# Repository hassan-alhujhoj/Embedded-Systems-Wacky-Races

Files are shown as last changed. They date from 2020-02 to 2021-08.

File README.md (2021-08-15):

Wacky Races Project
===================
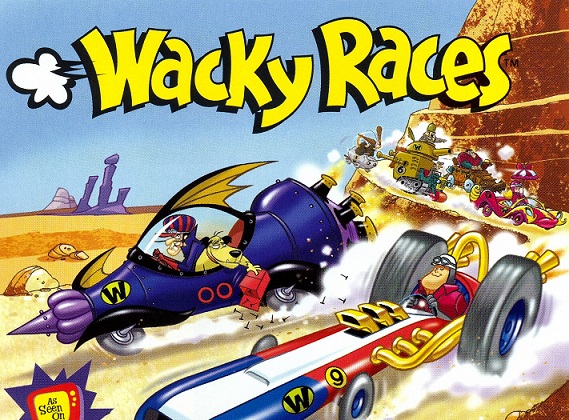
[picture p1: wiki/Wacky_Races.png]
Original_Series
.
[source](http://www.ps1fun.com/wacky-races)

Description
===========
This project was inspired by the infamous cartoon series Wacky Races which involves designing unique vehicles for each character that match their personalities. This project aimed to bring the series into an embedded systems reality.

The purpose of this assignment was to design, build, and program an embedded system using Atmel SAM4S8 microcontroller and surface mount technology. The goal of this assignment was to build the Wacky Racer (the driver board) and Wacky Hat (the vehicle controller) in Altium Designer, to populate the board using surface mount technologies (SMT), and to program the two boards in C to communicate with each other via nRF24 radio module.

This project was split into two groups: one group is responsible for the hat while the other work on the racer. Each group needed to design their board and work concurrently when collaboration is needed.

Project Outcome
===============
Participate in a Wacky Race and battle against other groups to eliminate them from the race.

Project Diagram
===============
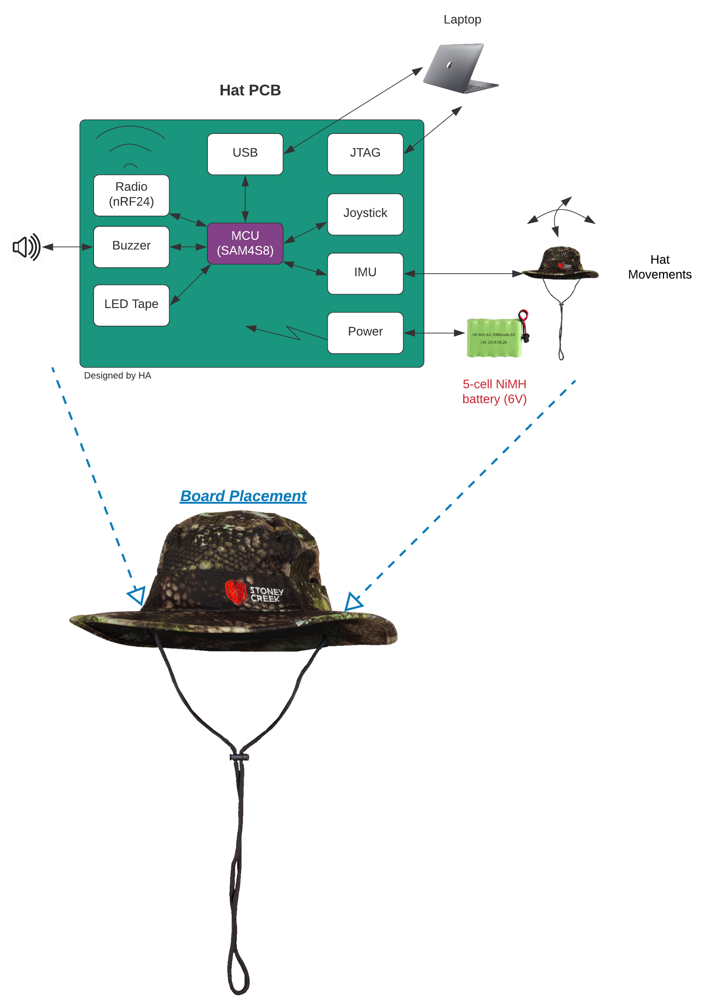
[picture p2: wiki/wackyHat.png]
hat

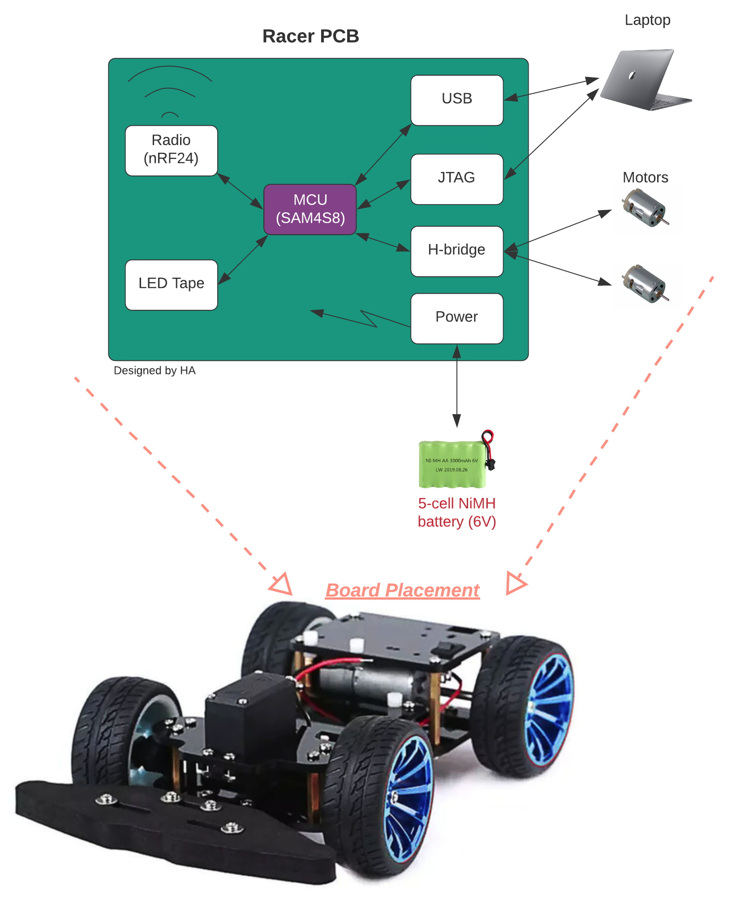
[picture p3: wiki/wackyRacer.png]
racer


Requirements
============
## Wacky Racer
* Must design a 4-layer PCB of dimension 85mmX64mm
* Use a USB interface for debugging
* Use a serial wire debug interface for MCU programming/debugging
* Must include an addequate fusing and reverse polarity protection
* Must have a sleep button
* Have afour jumber selected radio channels
* Interface with Wacky Hat board with a Nordic nRF24 SMD radio module
* Must include a low-battery-LED indicator
* Must be decorated with an LED tape controlled by the MCU
* Must regulate the nominal battery voltage to 5V with ADP2302ARDZ-50
* Drive the motors using H-briges (DRV8833)
* Use USB and JTAG interfaces for debugging

## Wacky Hat
* Must design a 4-layer PCB of dimension 85mmX64mm
* Use a USB interface for debugging
* Use a serial wire debug interface for MCU programming/debugging
* Must include an addequate fusing and reverse polarity protection
* Must have a sleep button
* Have afour jumber selected radio channels
* Interface with Wacky Hat board with a Nordic nRF24 SMD radio module
* Must include a low-battery-LED indicator
* Must be decorated with an LED tape controlled by the MCU
* Must regulate the nominal battery voltage to 5V with ADP2302ARDZ-50
* Use I2C IMU (MPU-9250) for head motion detection
* Use USB and JTAG interfaces for debugging

PCB Design
==========
doc_1doc_1  
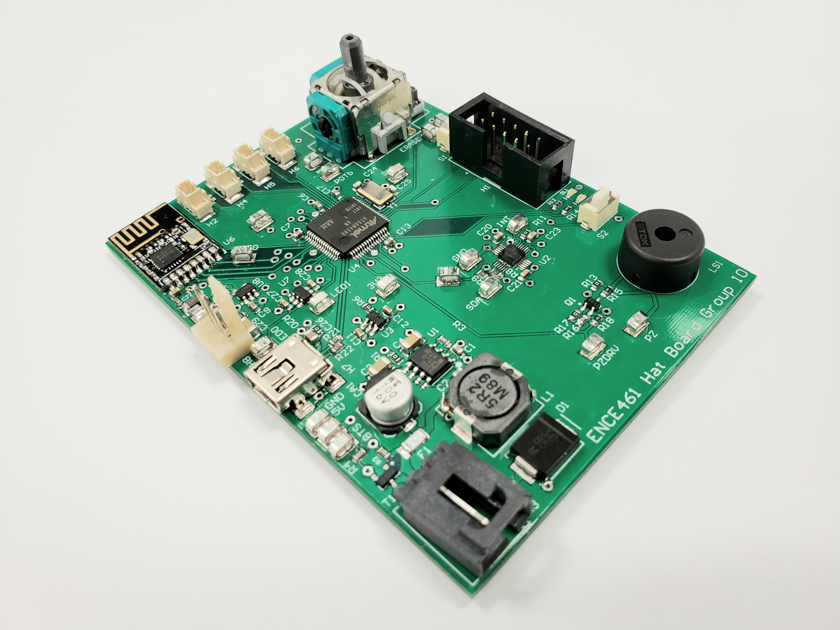
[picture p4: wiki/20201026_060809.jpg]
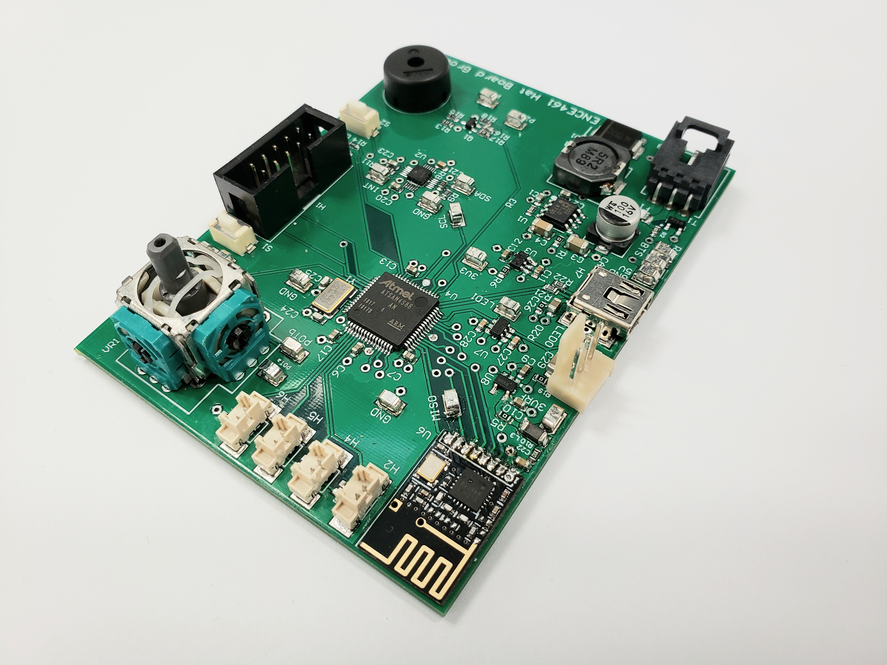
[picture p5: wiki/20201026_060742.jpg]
  

Contributors
============
* [Hassan Alhujhoj](https://github.com/hassan-alhujhoj)
* [Marcus Hughan](https://github.com/marcusHughan)
* [Nathan James](https://github.com/natedawgsnz)
* [Abdullah Naeem](https://eng-git.canterbury.ac.nz/ana104)

License
=======
Licensed under [MIT License](LICENSE)

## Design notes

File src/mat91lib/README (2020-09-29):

This library provides low level hardware abstraction for an AT91SAM7S
ARM microcontroller (with an ARM7TDMI ARM Thumb Processor).

These routines are design primarily for a bare-metal system.  The
philosophy is not to block (well at not least for long).

TODO
Convert files to use doxygen markup

Perhaps use CMSIS - Cortex Microcontroller Software Interface Standard

A note on handles.  These are designed to be opaque pointers or
integers and to provide a consistent interface.  This improves
portability but can be unnecessarily confusing.  Moreover, opaque
pointers hinder debugging.  In hindsight, I'd remove the opacity.

From a consistent interface point of view, the only exception is
pio_t.  Dereferencing a pointer stymies many optimisations, especially
for low performance microcontrollers.

adc_t
pwm_t
spi_t
ssc_t
tc_t
udp_t
usart_t

pio_t  (uint32)

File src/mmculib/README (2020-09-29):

Introduction:

This library (mmculib) contains a number of microprocessor independent
device drivers and miscellaneous functions.  It is primarily designed
for a bare-metal system.  mmculib relies on another library (such as
mat91lib) for microprocessor dependent support (such as low level
drivers for PIO, PWM. timer-counter (TC), etc.).

Compilation:

Here's an example of a Makefile to generate a program for the SAM4S16B
using mmculib and mat91lib.

# Executable file to create.
TARGET = target.bin

SRC = target.c foo.c bar.c

# Drivers from mmculib to use
DRIVERS = usb_cdc busart
# Peripherals from mat91lib to use
PERIPHERALS = ssc tc adc ac

# Microcontroller variety
MCU = SAM4S16B
# Link for ROM or RAM
RUN_MODE = ROM
# Optimisation options
OPT = -Os
# Path to mmculib top-level
MMCULIB_DIR = ../../mmculib
include $(MMCULIB_DIR)/mmculib.mk

The heavy-lifting is performed by the makefile fragment, mmculib.mk.
This automatically includes mat91lib.mk and the makefile fragments for
each driver and peripheral.

Other makefile variables that can be set to control the compilation are:
INCLUDES --- A list of paths to search for include files
VPATH    --- A list of paths to search for source files
CFLAGS   --- C compilation flags

Device driver API guidelines:

Each driver should support the following block read/write functions
where the addr parameter is optional.  Note the buffer is type void *
so that any object can be read/written without casting.  Len is the
transfer size in bytes.  The return value is the actual number of
bytes read or written.  Dev is a handle created by foo_init.  The
readv and writev forms are for reading/writing using a vector of
descriptors.  These forms are useful for coalescing I/O to minimise
writes (say to flash memory) or for atomic operations.

foo_ret_t
foo_read (foo_t dev, foo_addr_t addr, void *buffer, foo_size_t len);

foo_ret_t
foo_write (foo_t dev, foo_addr_t addr, const void *buffer, foo_size_t len);

foo_ret_t
foo_writev (foo_t dev, foo_addr_t addr, iovec_t *iov, iovec_count_t iov_count);

foo_ret_t
foo_readv (foo_t dev, foo_addr_t addr, iovec_t *iov, iovec_count_t iov_count);

Note, these routines should not block, well only for a very short time.

bits.h			Bit twidding macros
busart.c		Buffered USART driver
busart.h
button.c		Button/switch debouncing
button.h
buttons.c		Multiple button/switch debouncing
buttons.h
chaser.c		Sequenced flashing, uses flasher
chaser.h
ds18b20.c		Dallas one wire temperature sensor driver
ds18b20.h
ds2450.c		Dallas one wire ADC driver
ds2450.h
dscrc16.c		Dallas one wire 16 bit CRC
dscrc16.h
dscrc8.c		Dallas one wire 8 bit CRC
dscrc8.h
flasher.c		Generalised software PWM/flashing support
flasher.h
flasher_tweak.c		Run-time flasher manipulation
flasher_tweak.h
font.h			Font definition
isqrt16.c		16 bit integer square root
isqrt32.c		32 bit integer square root
lcd.c			HD44780/KS0066 LCD driver
lcd.h				
led.c			Simple LED driver
led_flash.c		LED flashing support
led_flash.h
led.h
lmatrix.c		LED matrix driver
lmatrix.h
mmelody.c		Interpret and sequence monophonic melodies
mmelody.h
mpwm.c
mpwm.h
mtext.c			Moving text driver
mtext.h
muxleds.c		Multiplexed LED driver
muxleds.h
nmea.c			NMEA string printing
nmea.h
nrf2401.c		Nordic RF driver
nrf2401.h
nrf_config.h
pga.c			Microchip PGA driver
pga.h		
piezo_beep.c		Piezo beep routines
piezo_beep.h
piezo.c			Simple piezo driver
piezo.h
rf.c			Generalised RF driver
rf.h
rf_master.c		Generalised RF master support
rf_slave.c		Generalised RF slave support
ring.c			Ring buffer
ring.h
scroller.c		Bit-mapped text scroller
scroller.h
s_eeprom.c		SPI EEPROM driver
s_eeprom.h
seq.c			Simple sequencer
seq.h
spwm.c
spwm.h
squeaker.c		Simple monophonic tune player
squeaker.h
stext.c			Simple text scroller (use mtext now)
stext.h
ticker.c		Simple polled timer
ticker.h
tweeter.c		PWM control of a piezo tweeter
tweeter.h
u1wire.c		Dallas universal one wire bus support
u1wire_debug.c		Dallas universal one wire bus debugging
u1wire_discover.c       Dallas universal one wire bus device discovery
u1wire_discover.h
u1wire.h
uint16toa.c		16-bit unsigned integer -> ASCII
uint16toa.h
uint8toa.c		8-bit unsigned integer -> ASCII
uint8toa.h

TODO
Convert files to use doxygen markup

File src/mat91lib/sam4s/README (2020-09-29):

Each MCU in sam4sxxxx.h defines SPI, PWM, TC0, for example 

#define SPI        ((Spi    *)0x40008000U)

The data structures are defined in Atmel/components/component_spi.h etc.

This is equivalent to the old AT91C_BASE_SPI

#define AT91C_BASE_SPI       (AT91_CAST(AT91PS_SPI) 	0xFFFE0000)

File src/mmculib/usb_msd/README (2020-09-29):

Perhaps the usb_sbc module is too coupled to usb_bot.

usb_bot requires callbacks for usb reading and writing.  Perhaps this
should be changed to non-blocking I/O.

usb_bot.c has too much MSD specific handling, for example, setup
requests, cbw, and csw stuff.

TODO, if the USB connection times out, say by using gdb, then
removing and reconnecting the USB does not properly work.

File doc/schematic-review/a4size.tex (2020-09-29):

% A4 210 mm x 298 mm
\pagestyle{plain}			% the default anyway
\pagenumbering{arabic}
\setlength{\oddsidemargin}{0mm}
\setlength{\evensidemargin}{-14mm}
\setlength{\marginparwidth}{0cm}
\setlength{\marginparsep}{0cm}
\setlength{\topmargin}{2mm}
\setlength{\headheight}{0mm}
\setlength{\headsep}{0cm}
\setlength{\textheight}{240mm}
\setlength{\textwidth}{168mm}
\setlength{\topskip}{0mm}
\setlength{\footskip}{10mm}
%
\setlength{\parindent}{8ex}

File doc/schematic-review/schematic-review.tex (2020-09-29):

\documentclass[a4paper, 12pt]{article}
\input a4size

\title{ENCE461 Schematic Review}
\author{M.P. Hayes}
\date{}

\begin{document}
\maketitle

\begin{center}
\textbf{Bring your schematics, printed on A3 paper}  
\end{center}

\section{Common}

\begin{enumerate}
\item Student names and group number in title block

\item Battery fusing (this is mandatory)

\item Can be powered from USB

\item Use serial wire debug interface for programming  

\item 3.3\,V MCU regulator can be back driven

\item Short circuit protection for MCU pio pins going to external headers

\item Battery voltage monitoring

\item Do the analogue inputs to the MCU exceed 3.3 V?  

\item LEDs for debugging  

\item Jumpers for mode configuration

\item Pullup resistors on TWI bus  
  
\item Test points

\item Ground test points

\item Game board interface connects to USART (TXD0/PA6 or TXD1/PA22 to
  TXD, RXD0/PA5 or RXD1/PA21 to RXD)

\item USB has series termination resistors

\item VBUS detection through voltage divider to PIO pin.  This is
  needed so that the MCU can tell when USB is plugged in or removed.
  You will also need diodes (or jumpers) so that the USB 5\,V can be
  connected to the 5\,V from the switching regulator.

\item Power supply filtering for radio (recommend ferrite bead or
  resistor in series with power rail with parallel capacitor)

\item The radio needs to be connected to SPI pins (MISO/PA12,
  MOSI/PA13, SCK/PA14)

\item TWI uses TWCK0/PA4 and TWD0/PA3 or TWCK1/PB5 and TWD1/PB4.
  
\item SAM4S erase pin on testpoint

\item SAM4S has 12\,MHz crystal

\item Reset button connected to NRST pin

\item Power on/off button connected to WKUPn pin

\item Avoid PB4--PB5 for general I/O (they default to JTAG pins on
  reset but can be reconfigured in software)

\item Have external pull-down resistors to ensure chips are disabled on
  power-up

\item Have a few spare PIO pins connected to pads for last minute mods.  
  
\end{enumerate}

\section{Hat board}

\begin{enumerate}
\item Battery can be charged from USB
  
\item Fall-back option if IMU does not work

\item Nav-switch or joystick for remote control  
  
\item Drive circuit for piezo tweeter

\end{enumerate}

\section{Racer board}

\begin{enumerate}
\item Fall-back option to drive motors via servo interface using PWM
  if H-bridge driver fails
  
\item MOSFET(s) for actuator (if use p-channel MOSFET need transistor
  to provide sufficient gate voltage to turn MOSFET off)

\item H-bridge driven by four PWM signals (it is best to use PWMHx,
  note PWMLx and PWMHx are complementary)

\item H-bridge AISEN and BISEN pins connected to ground (unless using
  current control)

\end{enumerate}

\end{document}

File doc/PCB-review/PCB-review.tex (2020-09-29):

\documentclass[a4paper, 12pt]{article}
\usepackage{url}

\input a4size

\title{ENCE461 PCB Review}
%\author{M.P. Hayes}
\author{}
\date{}

\begin{document}
\maketitle

\begin{center}
  \textbf{Bring this checklist, annotated with ticks or question
    marks, a printout of your new schematics, and the schematics
    annotated at the schematic rewiew.}
\end{center}

\section*{Schematic}

\begin{enumerate}
\item Battery is fused before any other electrical connection

\item Battery has reverse polarity protection (hat board only)

\item 3.3\,V for game board is provided by LDO regulator connected to
  battery on hat board

\item Radio has power supply filtering

\item Game board RX pin (3) connected to SAM4S USART RXD (PA5, PA21), and TX pin
  (5) connected to SAM4S USART TXD.

\end{enumerate}

\section*{Silk screen layer}

\begin{enumerate}
\item Has group number

\item Has student names

\item Has clearly labelled test points

\item Has clearly labelled battery polarity for hat board

\item Has clearly labelled connectors  

\end{enumerate}

\section*{Mechanical}

\begin{enumerate}
\item Drill sizes meet requirements (min 0.3, steps of 0.1)

\item USB connector hangs over edge correctly
  
\item Radio antenna hangs over edge or there are cut-outs in the PCB planes  
\end{enumerate}

\pagebreak

\section*{Plane layers}

\begin{enumerate}
\item Has a ground plane
  
\item The ground plane is connected to the GND net

\item Has a power plane (this can be partitioned)

\item The power planes are connected to the appropriate power nets

\item Has cut outs for the radio antenna if the antenna does not hang
  over edge
\end{enumerate}

\section*{Signal layer}

\begin{enumerate}
\item All vias go from top to bottom layers

\item There are no long power/ground traces to planes (use more vias)
  
\item Large vias and wide traces are used for power/ground and
  high-current traces
  
\item IC pins are not connected between the pads
  
\item SPI, I2C, PWM, and UART signals do not run over gaps in a plane

\item SPI, I2C, PWM, and UART signals do not change layers more than twice

\item Ground test points are positioned for ease of use
\end{enumerate}

\section*{Design rule check}

\begin{enumerate}
\item There are no clearance violations when performing a design rule check

\item There are no trace width violations when performing a design rule check  

\item There are no unrouted nets  
\end{enumerate}  

Note, Altium gets confused with the pad to plane check when adding
decoupling caps, so ignore warnings with distances of 2.5\,m.

\section*{Further checks}

See
\url{http://ecewiki.elec.canterbury.ac.nz/mediawiki/index.php/PCB_guidelines}
and
\url{http://ecewiki.elec.canterbury.ac.nz/mediawiki/index.php/PCB_advanced_guidelines}.

\end{document}

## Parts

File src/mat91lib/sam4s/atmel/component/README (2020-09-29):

These files define a structure for each peripheral but not their bases
addresses.  The structures are named Spi, Pwm, etc.

Spi is equivalent to the old AT91PS_SPI.

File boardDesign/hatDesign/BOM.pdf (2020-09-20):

Bill of Materials | Bill of Materials for PCB Document [HatBoard_Group10.PcbDoc]
Source Data From: | | HatBoard_Group10.PcbDoc
Project: | | WackyRacesHat.PrjPcb
Variant: | | None
Creation Date: | 22/06/2020 | 11:10 PM
Print Date: | 22-Jun-20 | 11:11:22 PM
Footprint | Comment | LibRef | Designator | Description | Quantity
CAPC1608L | 100nF | CC_100nF_0603 | C1, C2, C5, C6, C7, C8, C13, C14, C15, C16, C17, C19, C20, C23 | CAP CER 100nF X7R +-10% 50V 0603 | 14
CAPC3216L | 22uF | CC_22uF_1206 | C3, C4, C29 | CAP CER 22uF Y5V -20% +80% 10V 1206 | 3
CAPC1608L | 1uF | CC_1uF_0603 | C9, C10, C11, C12 | CAP CER 1uF Y5V -20% +80% 16V 0603 | 4
CAPC1608N | 4.7uF | CC_4.7uF_0603 | C18, C26 | CAP CER 4.7uF X5R +-20% 10V 0603 | 2
CAPC1608L | 10nF | CC_10nF_0603 | C21, C27, C28 | CAP CER 10nF X7R +-10% 50V 0603 | 3
CAPC1608L | 10uF | CC_10uF_0603 | C22 | CAP CER 10UF X5R +-20% 6V3 0603 | 1
CAPC1608L | 27pF | CC_27pF_0603 | C24, C25 | CAP CER 27pF NPO/COG +-5% 50V 0603 | 2
NICH-1 | 100uF/16V | CA_100uF_16V | CA1 | CAP ALUM 100uF 16V SMD | 1
SMC | VS-30BQ015-M3/9AT | DS_VS-30BQ015-M3 | D1 | DIODE, SCHOTTKY, 3A, 15V, DO-214AB / SMC | 1
WL-SMCW0603 | Bright Green | DL_150060VS75000 | DL1 | LED Bright Green 40mcd 0603 SMD | 1
WL-SMCW0603 | Red | DL_150060RS75000 | DL2 | LED Red 250mcd 0603 SMD | 1
RESC3216N | 5A | FS_Fuse_5.0A | F1 | Fuse 5.0A Fast Acting 1206 SMD | 1
IDC2.54-V10D | Header 5X2 Vert | JA_HDR_IDC_5X2_VERT | H1 | IDC Header, 2,54mm, 10-Pin, Vert | 1
SD-53398-0219 | SMD Vert 1.25mm | JB_53398-02 | H2, H4, H5, H6 | Header_Vert_2Pos_1.25mm_125V@1A_SMT | 4
BATT_HEADER_3POS | Battery_HEADER_3pin | Battery_HEADER_3pin | H3 | 3Pin Header 2.54mm spacing | 1
USB/SM0.8-6H5 | JS_USB_MINI_B | JS_USB_MINI_B_SMT | H7 | USB 2.0, Right Angle, SMT, B Type, Receptacle, 5 Position, | 1
HEADER_3POS | HEADER_3 | HEADER_3 | H8 | 3Pin Header 2.54mm spacing | 1
INDUCTOR5u2 | IND 5.2UH 6A | CDRH104RNP-5R2NC | L1 | FIXED IND 5.2UH 6A 22 MOHM SMD | 1
INDC3216L | 1A max, Idc 0.3R, | IN_Ferrite-Bead | L2, L3 | Ferrite Bead, Rdc 0.3R, Z100MHZ 600R, Imax 1A, SMD 1206 | 2
XDCR_PS1240P02BT | PS1240P02BT | PS1240P02BT | LS1 | Buzzers Transducer, Externally Driven Piezo 3V 4kHz 60dB @ 3V, 10cm Through Hole PC Pins | 1
SOT323_M | BC817W | TB_BC817W | Q1 | NPN GP Bipolar Transistor 45V 500mA SOT323 | 1
RESC1608L | 0R | RS_0R0 | R1, R5, R6, R11, R13, R17, R19, R20 | RES 0.0 OHM 1/10W 5% 0603 SMD | 8
RESC1608L | 200K | RS_200K | R2 | RES 200K OHM 1/10W 5% 0603 SMD | 1
RESC1608L | 100K | RS_100K | R3, R4 | RES 100K OHM 1/10W 5% 0603 SMD | 2
RESC3216L | 1R | RT_1R | R7 | RES 1R OHM 1/4W 5% 1206 SMD | 1
RESC1608L | 2K2 | RS_2K2 | R8, R9 | RES 2.2K OHM 1/10W 5% 0603 SMD | 2
RESC1608L | 10R | RS_10R | R10, R16 | RES 10 OHM 1/10W 5% 0603 SMD | 2
RESC1608L | 470R | RS_470R | R12 | RES 470 OHM 1/10W 5% 0603 SMD | 1
RESC1608L | 680R | RS_680R | R14 | RES 680 OHM 1/10W 5% 0603 SMD | 1
RESC1608L | 1K | RS_1K | R15, R18 | RES 1.0K OHM 1/10W 5% 0603 SMD | 2
RESC1608L | 27R | RS_27R | R21, R22 | RES 27 OHM 1/10W 5% 0603 SMD | 2
EVQPNF05M | EVQPNF05M | WS_EVQPNF05M | S1, S2 | Panasonic 6 x 3.5mm SMD Light Touch Switch Type SMD | 2
SOT23_L | BSH105,215 | TM_BSH105 | T1 | MOSFET N-CH 20V 1.05A SOT-23 | 1
RD_8_1 | ADP2302ARDZ-5.0 BUCK | ADP2302ARDZ-5.0-R7 | U1 | IC REG BUCK 5V 2A 8SOIC | 1
QUAD24 | MPU-9250 | MPU-9250 | U2 | 9 axis IMU | 1
SOT95P280X145-5N | CAT6219-330TDGT3 | SV_CAT6219-330TDGT3 | U3, U8 | IC REG LIN 3.3V 500MA TSOT23-5 | 2
LQFP64_L | ATSAM4S8BA-ANR | SE_ATSAM4S16BA-MU | U4 | IC MCU 32BIT 512KB FLASH 64LQFP | 1
NRF24 | nRF24 SMD | NRF24 | U6 | nRF24 SMD Module | 1
SOT23-6_N | SN74LVC1T45 | SN74LVC1T45 | U7 | 1.8V - 5V level converter | 1
Joystick_Sw | Joystick 10k with Sw | Joystick 10k with Sw | VR1 | JOYSTICK 10K OHM 2 AXIS TH | 1
6.0X3.5-4 | 12MHz | XT_CRYSTAL_12MHz_18pF | Y1 | CRYSTAL 12MHZ 18PF 6X3.5mm SMD | 1
| | | | | 81
Approved | | Notes
Altium Limited Confidential | 22/06/2020 | Page 1

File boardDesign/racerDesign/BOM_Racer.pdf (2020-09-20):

Bill of Materials | Bill of Materials for PCB Document [WackyRacerPCB.PcbDoc]
Source Data From: | | WackyRacerPCB.PcbDoc
Project: | | WackyRacerDesign.PrjPcb
Variant: | | None
Creation Date: | 18/06/2020 | 4:25 PM
Print Date: | 18-Jun-20 | 4:25:29 PM
Footprint | Comment | LibRef | Designator | Description | Quantity
SOT95P280X145-5N | CAT6219-330TDGT3 | SV_CAT6219-330TDGT3 | 3V3_REG, 3V3RF_REG | IC REG LIN 3.3V 500MA TSOT23-5 | 2
RD_8_1 | ADP2302ARDZ-5.0 BUCK | ADP2302ARDZ-5.0-R7 | BUCK | IC REG BUCK 5V 2A 8SOIC | 1
MOLEX_KK_2_HDR | 2 Pin Molex KK HDR | JA_MOLEX_KK_2POS | Bumper, CH1, CH2, CH3, CH4, M_1, M_2, M_3 | CONN HEADER 2POS 2.54mm VERT_Thru Hole | 8
CAPC1608L | 10uF | CC_10uF_0603 | C1, C4, C10, C25 | CAP CER 10UF X5R +-20% 6V3 0603 | 4
CAPC1608L | 27nF | CC_27nF_0603 | C2, C3 | CAP CER 27nF X7R +-10% 50V 0603 | 2
CAPC1608L | 100nF | CC_100nF_0603 | C5, C12, C13, C14, C15, C16, C17, C18, C19, C22, C24, C26, C30, C31 | CAP CER 100nF X7R +-10% 50V 0603 | 14
CAPC3216L | 22uF | CC_22uF_1206 | C6, C7 | CAP CER 22uF Y5V -20% +80% 10V 1206 | 2
CAPAE6666X77M | 100µF/25V | CA_100uF_25V | C8 | CAP ALUM 100UF 25V 20% SMD | 1
CAPC1608L | 10nF | CC_10nF_0603 | C9 | CAP CER 10nF X7R +-10% 50V 0603 | 1
CAPC1608L | 2.2uF | CC_2.2uF_0603 | C11, C27 | CAP CER 2.2uF X5R +-20% 10V 0603 | 2
CAPC1608L | 1uF | CC_1uF_0603 | C20, C21, C28, C29 | CAP CER 1uF Y5V -20% +80% 16V 0603 | 4
CAPC1608N | 4.7uF | CC_4.7uF_0603 | C23, C32 | CAP CER 4.7uF X5R +-20% 10V 0603 | 2
SMC | SCHOTTKY 30V 4A | MBRS330T3G | D1 | DIODE SCHOTTKY 30V 4A SMC | 1
WL-SMCW0603 | Dark Green | DL_150060GS75000 | DL1 | LED Dk Green 430mcd 0603 SMD | 1
WL-SMCW0603 | Red | DL_150060RS75000 | DL2 | LED Red 250mcd 0603 SMD | 1
RESC3216N | 5A | FS_Fuse_5.0A | F1 | Fuse 5.0A Fast Acting 1206 SMD | 1
IDC2.54-V10D | Header 5X2 Vert | JA_HDR_IDC_5X2_VERT | H1 | IDC Header, 2,54mm, 10-Pin, Vert | 1
BATT_HEADER_3POS | Battery_HEADER_3pin | Battery_HEADER_3pin | H3 | 3Pin Header 2.54mm spacing | 1
HEADER_3POS | HEADER_3 | HEADER_3 | H4 | 3Pin Header 2.54mm spacing | 1
HTSOP16 | DRV8833 | DRV8833 | H-Bridge_1, H-Bridge_2 | Dual H-Bridge Motor Driver 1.5A | 2
INDC3216L | 1A max, Idc 0.3R, | IN_Ferrite-Bead | L1, L3 | Ferrite Bead, Rdc 0.3R, Z100MHZ 600R, Imax 1A, SMD 1206 | 2
INDUCTOR5u2 | IND 5.2UH 6A | CDRH104RNP-5R2NC | L2 | FIXED IND 5.2UH 6A 22 MOHM SMD | 1
TP_0603 | =Value | TP_0603 | LED_IN1, MOSI, SCK | Test Point 1.65X0.9X1.2mm SMD | 3
MOLEX_KK_3_HDR | 3 Pin Molex KK Hdr | JA_MOLEX_KK_3POS | LED_TAPE | CONN HEADER 3POS 2.54mm VERT_Thru Hole | 1
SOT23-6_N | SN74LVC1T45 | SN74LVC1T45 | LVL_CON | 1.8V - 5V level converter | 1
TP_0603 | TP_0603 | TP_0603 | MISO | Test Point 1.65X0.9X1.2mm SMD | 1
NRF24 | nRF24 SMD | NRF24 | nRF24 | nRF24 SMD Module | 1
SOT23_L | SSM3J328R,LF | TM_SSM3J328R | Q1 | MOSFET P-CH 20V 6A SOT23-3 | 1
RESC1608L | 10R | RS_10R | R1 | RES 10 OHM 1/10W 5% 0603 SMD | 1
RESC1608L | 27R | RS_27R | R2, R3 | RES 27 OHM 1/10W 5% 0603 SMD | 2
RESC1608L | 100R | RS_100R | R4, R6 | RES 100 OHM 1/10W 5% 0603 SMD | 2
RESC1608L | 1K3 | RS_1K3 | R7 | RES 1.3K OHM 1/10W 5% 0603 SMD | 1
RESC1608L | 100K | RS_100K | R8, R9 | RES 100K OHM 1/10W 5% 0603 SMD | 2
RESC1608L | 0R | RS_0R0 | R10, R11, R13, R14 | RES 0.0 OHM 1/10W 5% 0603 SMD | 4
RESC3216L | 1R | RT_1R | R12 | RES 1R OHM 1/4W 5% 1206 SMD | 1
RESC1608L | 470K | RS_27R, RS_47R | R15, R19 | RES 27 OHM 1/10W 5% 0603 SMD, RES 47 OHM 1/10W 5% 0603 SMD | 2
RESC1608L | 270K | RS_27R, RS_47R | R16, R18 | RES 27 OHM 1/10W 5% 0603 SMD, RES 47 OHM 1/10W 5% 0603 SMD | 2
RESC1608L | 10K | RS_10K | R17, R20 | RES 10.0K OHM 1/10W 5% 0603 SMD | 2
EVQPNF05M | EVQPNF05M | WS_EVQPNF05M | S1, S2 | Panasonic 6 x 3.5mm SMD Light Touch Switch Type SMD | 2
LQFP64_L | ATSAM4S8BA-ANR | SE_ATSAM4S16BA-MU | U1 | IC MCU 32BIT 512KB FLASH 64LQFP | 1
MOLEX_KK_4_HDR | Ultrasonic Sensor Connector | JA_MOLEX_KK_4POS | US | CONN HEADER 4POS 2.54mm VERT_Thru Hole | 1
FCI_USB_10118194-0001LF | JS_USB_MICRO_B | JS_USB_MICRO_B_SMT | USB | CONN USB MICRO B RECPT SMT R/A | 1
6.0X3.5-4 | 12MHz | XT_CRYSTAL_12MHz_18pF | Y1 | CRYSTAL 12MHZ 18PF 6X3.5mm SMD | 1
| | | | | 88
Approved | | Notes
Altium Limited Confidential | 18/06/2020 | Page 1

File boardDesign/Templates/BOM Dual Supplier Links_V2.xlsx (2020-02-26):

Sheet: BOM Report
Bill of Materials |  |  | Field=Title
Source Data From: |  | Field=DataSourceFileName
Project: |  | Field=ProjectFileName
Variant: |  | Field=VariantName
Creation Date: | Field=ReportDate | Field=ReportTime
Print Date: | 2015-03-04 | 16:44:09
Production Quantity: | Field=ProductionQuantity
Currency | Field=Currency
Column=Footprint | Column=Comment | Column=LibRef | Column=Designator | Column=Description | Column=Quantity | Column=Supplier 1 | Column=Supplier Part Number 1 | Column=Supplier 2 | Column=Supplier Part Number 2 | Column=Manufacturer | Column=Manufacturer Part Number | Column=Manufacturer PN | Column=Supplier Stock 1 | Column=Supplier Stock 2
 |  |  |  |  | 0
Approved |  | Notes

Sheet: Project Information
Project Full Path | Field=ProjectFullPath
Project Filename | Field=ProjectFileName
Variant Name | Field=VariantName
Data-Source Filename | Field=DataSourceFileName
Data-Source Full Path | Field=DataSourceFullPath
Title | Field=Title
Total Quantity | Field=TotalQuantity
Report Time | Field=ReportTime
Report Date | Field=ReportDate
Report Date & Tine | Field=ReportDateTime
Output Name | Field=OutputName
Output Type | Field=OutputType
Output Generator Name | Field=GeneratorName
Output Generator Description | Field=GeneratorDescription

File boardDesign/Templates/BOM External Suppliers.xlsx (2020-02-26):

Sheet: BOM Report
Bill of Materials |  |  | Field=Title | BOM of externally supplied components
Source Data From: |  | Field=DataSourceFileName
Project: |  | Field=ProjectFileName
Variant: |  | Field=VariantName
Creation Date: | Field=ReportDate | Field=ReportTime
Print Date: | 2013-08-14 | 15:08:35
Column=LibRef | Column=Comment | Column=Footprint | Column=Designator | Column=Description | Column=Quantity | Column=Manufacturer | Column=Manufacturer Part Number 1 | Column=Supplier 1 | Column=Supplier Part Number 1 | Column=Supplier 2 | Column=Supplier Part Number 2 | Column=Supplier 3 | Supplier Part Number 3
 |  |  |  |  | 0
Approved |  | Notes

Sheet: Project Information
Project Full Path | Field=ProjectFullPath
Project Filename | Field=ProjectFileName
Variant Name | Field=VariantName
Data-Source Filename | Field=DataSourceFileName
Data-Source Full Path | Field=DataSourceFullPath
Title | Field=Title
Total Quantity | Field=TotalQuantity
Report Time | Field=ReportTime
Report Date | Field=ReportDate
Report Date & Tine | Field=ReportDateTime
Output Name | Field=OutputName
Output Type | Field=OutputType
Output Generator Name | Field=GeneratorName
Output Generator Description | Field=GeneratorDescription

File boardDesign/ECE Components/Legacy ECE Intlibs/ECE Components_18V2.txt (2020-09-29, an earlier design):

Created using AD18.1.7 (Build 191)
Tested using AD16.1.10 (Build 233) - 2018 ECE Dept installed version.

28 AUGUST 2018
***ECE Components_18V2.IntLib***
ADD - FS_FUSE_10A smd fuse 
FIX - JA_TERM_BLK_HDR2 - E14 manufacturer & part numbers mixed. Added Digikey data
DEL - Remove 100nF 0402 cap.
DEL - DS_VS_30BQD015TRPBF - obsolete
ADD - DS_VS_30BQ015-M3 - replacement for DS_VS_30BQD015TRPBF
FIX - TM_SSM3J328R - update parameters VDSS & ID(dc). Fix part#. Add datasheet
FIX - WS_EVQPNF05M - increase footprint pads 2x1.6 -> 2.5x1.6. Allows rework.
FIX - FS_FUSE_5.0A - obsolete, remove old & add new part data & links
FIX - DR_BAS16TT1G - Fix E14 part #, add  Digikey data
FIX - XT_CRYSTAL - correct the Digikey supplier information + links
FIX - WS_SKUDBE010 - Nav switch - correct footprint pad spacing
ADD - TP_1206 - add 3d model
DEL - JP_1613 14 DC socket - obsolete
ADD - JP_PJ-002AH-SMT-TR - replaces JP_1613 14. 
FIX - JP_PJ-002AH-SMT-TR - Redraw schematic symbol - this was incorrect on obsolete part also (switching is on outer barrel not inner pin).
FIX - CA_470uF_16V - replace incorrect E14 parameters - add Digikey part info
FIX - CA_1000uF_16V - add Digikey info
FIX - JS_USB_MICRO_B_SMT - corrected footprint minimum width violation. Improved pad shape on GNDs for better strain relief and easier rework. Adj silkscreen.
ADD - JA_HDR_IDC_3X2_VERT - 6 PIN 0.1" IDC through hole connector + supplier data
ADD - IDC2.54-V06D 6PIN-IDC footprint and 3D model - Linked to JA_HDR_IDC_3x2_VERT
FIX - SV_TLV1117-33CDC add note to schematic symbol that warns about relatively high Vdropout at full load
FIX - SV_TLV1117-50CDC add note to schematic symbol that warns about relatively high Vdropout at full load

Previous updates:

***ECE_Components_16_2.IntLib***
-JB_IDC_BOX_HDR_10, schematic symbol pinout corrected
-SV_LD29300 removed - obsolete

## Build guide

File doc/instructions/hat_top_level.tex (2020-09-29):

\begin{tikzpicture}[scale=0.9]
    
  \draw[black, very thick, fill=blue!50] (-2, -1) rectangle (2, 1);
    \node at (0, 0) {SAM4S};  

    % IMU
    \draw[black, very thick] (4, -1) rectangle (7, 1);
    \node at (5.5, 0) {IMU};
    \draw[triangle 45-triangle 45] (2, 0) -- (4, 0);

    % Buzzer
    \draw[black, very thick] (4, -2) rectangle (7, -4);
    \node at (5.5, -3) {Buzzer};
    \draw[-triangle 45] (2, -1) -- (4, -2);

    % LED tape
    \draw[black, very thick] (-2, 2) rectangle (2, 4);
    \node at (0, 3) {LED tape};
    \draw[triangle 45-triangle 45] (0, 1) -- (0, 2);

    % Radio
    \draw[black, very thick] (-2, -2) rectangle (2, -4);
    \node at (0, -3) {Radio};
    \draw[triangle 45-triangle 45] (0, -1) -- (0, -2);
    \draw (0.354, -4.354) arc (-45:-135:0.5);
    \draw (0.707, -4.707) arc (-45:-135:1);
    \draw (1.061, -5.061) arc (-45:-135:1.5);

    % Power
    \draw[black, very thick] (-4, 2) rectangle (-7, 4);
    \node at (-5.5, 3) {Power};
    \draw (-5, 2) -- (-5.25, 1.4) -- (-4.75, 1.6) -- (-5, 1);
    \draw (-6, 2) -- (-6.25, 1.4) -- (-5.75, 1.6) -- (-6, 1);
    
    % USB
    \draw[black, very thick] (-4, -2) rectangle (-7, -4);
    \node at (-5.5, -3) {USB};
    \draw[triangle 45-triangle 45] (-2, -1) -- (-4, -2);

\end{tikzpicture}

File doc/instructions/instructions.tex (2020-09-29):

\documentclass[11pt, a4paper]{article}
\title{Wacky Racers 2020 Instructions}
\author{Michael Hayes, Ben Mitchell}
\date{Version 3, \today}

\usepackage[margin=1in]{geometry}
\usepackage{parskip}
\usepackage{float}
\usepackage{todonotes}
\presetkeys{todonotes}{inline}{}
\usepackage{graphicx}
\usepackage[T1]{fontenc}
\usepackage{makecell}
\usepackage[breaklinks=true]{hyperref}
\usepackage{tabularx}
\usepackage{subcaption}
\usepackage{listings}
\usetikzlibrary{arrows}

\newcommand{\code}[1]{\texttt{#1}}

\begin{document}
\maketitle

\section{Introduction}

The purpose of this assignment is to design, build, and program an
embedded system using an ARM microcontroller and surface mount
technology.

The goal for each group of four students is to build a remote
controlled vehicle (the Wacky Racer) and its controller (the Wacky
Hat).  At the conclusion of the assignment there will be a dastardly race!

Each group is comprised of two sub-groups of two students.  One of
these subgroups constructs the Wacky Racer and the other constructs
the Wacky Hat.  You may be asking why is the Wacky Hat called the
Wacky Hat?  Well, a hat that controls a remote vehicle using head
motions is not an ordinary hat!

\section{Requirements}

The following requirements are mandatory if you wish to maximise your
marks.

\subsection{Wacky racer}

\begin{enumerate}
\item The chassis is to be constructed by each group.  These can be
  3-D printed, constructed from Perspex or wood, etc.  A standard
  chassis is available from the Automation Lab technician (Daniel
  Hopkins).  The electronics must be visible on top of the chassis.
\item Have a standard working bump sensor (supplied).  
\item Locomotion can only use two 6\,V DC motors (supplied).
\item Everything must be powered from a single 5-cell NiMH battery pack (supplied).
\item Use a single four layer printed circuit board of dimension 85\,mm$\times$64\,mm.
\item Use an ARM microcontroller (Atmel SAM4S8).
\item Drive the motors using H-bridges (Texas Instruments DRV8833 dual
  H-bridge is recommended).
\item Regulate the nominal battery voltage to 5\,V with a buck
  regulator IC (ADP2302ARDZ-50).
\item Be decorated with an LED tape (supplied) controlled by the MCU.
\item Use a USB interface for debugging.
\item Use a serial wire debug interface for MCU programming/debugging.
\item Have adequate battery fusing and reverse polarity protection.
\item Have a sleep button.
\item If the battery voltage drops below 5\,V, an LED should flash and high power draw devices should be disabled.
\item Interface to the Wacky Hat with a Nordic nRF24 SMD radio module.
\item Have four jumper selectable radio channels.  
\item Have a mounted RFID card (supplied) that can be read by the Wacky ramps.
\item Be humorous.    
\end{enumerate}

Each Wacky Racer can have a dastardly means of hindering another
team's Wacky Racer.  However, you cannot:
%
\begin{itemize}
\item Damage or destroy another Wacky racer
\item Damage the venue
\item Injure a spectator
\item Jam the radio signals  
\end{itemize}

\vspace{1cm}

\begin{figure}[h]
    \centering
    \input{racer_top_level.tex}
    \caption{Racer board top level diagram.}
\end{figure}

\vfill\pagebreak

\subsection{Wacky hat}

\begin{enumerate}
\item Construct a Wacky Hat that contains all the electronics.
\item Everything must be powered from a single 5-cell NiMH battery pack (supplied).  
\item Have adequate battery fusing and reverse polarity protection.
\item Use a single four layer printed circuit board of dimension 85\,mm$\times$64\,mm.  
\item Use an ARM microcontroller (Atmel SAM4S8).
\item Regulate the nominal 6\,V battery voltage to 5\,V with a buck
  regulator IC (ADP2302ARDZ-50).
\item Be decorated with an LED tape (supplied) controlled by the MCU.
\item Use an I2C IMU (MPU-9250) for head motion detection.
\item Use a USB interface for debugging.
\item Use a serial wire debug interface for MCU programming/debugging.
\item Have a joystick in case the IMU does not work.
\item Have a sleep button.
\item If the battery voltage drops below 5\,V, an LED should flash and high power draw devices should be disabled.
\item Play sound when the bumper is hit.
\item Interface to the Wacky Racer with a Nordic nRF24 SMD radio module.  
\item Have four jumper selectable radio channels.    
\item Be humorous.  
\end{enumerate}

%\vspace{1cm}

\begin{figure}[h]
  \centering
  \input{hat_top_level.tex}
  \caption{Racer hat top level diagram.}
\end{figure}

\pagebreak

\section{Assignment schedule}

The planned activities for the timetabled labs in the Embedded Systems
Lab (ESL) are:
%
\begin{flushleft}
  \begin{tabular}{ c l l }
    Week            &  Assistance  &  Assessment \\
    \hline \hline
    T1-1 & Altium tutorial 1 (schematics)  & \\
    T1-2 & Altium help       & \\
    T1-3 & Schematic review  &  Schematic submission for review (Mon. noon) \\
    T1-4 & Altium tutorial 2 (PCB) &          \\
    T1-5 & Altium help & PCB submission 1    \\
    T1-6 & Altium help & PCB submission 2    \\
    T1-7 & General     & PCB submission 3    \\ \hline
    B-1 & (break)    &                   \\
    B-2 & (break)    &                   \\
    B-3 & (break)    &                   \\ \hline
    T2-1 & General     & Blinky            \\
    T2-2 & General     & IMU/motors      \\
    T2-3 & General     & Radio control     \\    
    T2-4 & General     & Functionality     \\
    T2-5 & Competition & Competition, critique  \\
  \end{tabular}
\end{flushleft}

Notes:
%
\begin{enumerate}
\item There there may be a 6--10 day delay for the PCBs to be
  manufactured from the time of submission.  You will then need to
  book an assembly session in the SMT lab provided you have done the
  SMT lab induction.

\item Do not underestimate the blinky milestone.  It requires having a
  functional PCB with a microcontroller that turns on properly, a
  functional toolchain and the ability to download code into the
  microcontroller's flash memory.
\end{enumerate}

\section{Assessment}

The marks breakdown (max. 0x64) is:
%
\begin{flushleft}
  \begin{tabular}{ll}
    PCB submission & 0--0xa marks\\
    Blinky milestone  & 0x5 marks\\    
    IMU/motor milestone  & 0x5 marks\\
    Radio control milestone  & 0x5 marks\\
    Functional assessment & 0--0x14 marks \\
    Board inspection & 0--0x1e marks \\
    Competition & 0--0xa marks \\
    Individual critique & 0--0xf marks \\
  \end{tabular}
  
\end{flushleft}

\subsection{Milestones}

There are five milestones.  To achieve the associated marks, they must
be demonstrated to a T.A. by the end of the lab for your allotted
stream.  If you need an exception to this, see Ben Mitchell with a
\emph{very} good reason.  The milestone requirements are:
%
\begin{description}
\item [Schematic review] Submit your A3 schematic on Learn for
  review.  Lose 10 marks if you miss the submission time.

\item [PCB submission] Submit your PCB design to Learn for
  manufacture.  To encourage early submission there is a sliding scale
  for marks depending on when the PCB is submitted, see table.  After
  week 7, there is a 10 mark penalty per week.  \textbf{NB, a rushed
    PCB design will cause you more grief, more PCB rework, and a lower
    mark for the inspection.}

  \begin{tabular}{llll}
    Week & Submission day & Cut-off time  & Mark \\ \hline
    5    & Monday       & 10.00 am & 10 \\
    5    & Wednesday    & 10.00 am & 9 \\
    5    & Friday       & 10.00 am & 8 \\
    6    & Monday       & 10.00 am & 7 \\
    6    & Wednesday    & 10.00 am & 6 \\
    6    & Friday       & 10.00 am & 5  \\
    7    & Monday       & 10.00 am & 4 \\
    7    & Wednesday    & 10.00 am & 2 \\
    7    & Friday       & 10.00 am & 0 \\        
  \end{tabular}

\item [Blinky] Demonstrate that can blink an LED controlled by the SAM4S.
  
\item [IMU/motors] For the Wacky Hat, demonstrate output of IMU
  readings to a PC using USB CDC.  For the Wacky Racer, demonstrate
  control of the motors from a PC using USB CDC.

\item[Radio control] Demonstrate sending commands from the Wacky Hat
  to the Wacky Racer over a radio link.
\end{description}

\textbf{If you cannot show the functionality of a previous milestone
  during any assessment, you will fail that assessment and loose any
  marks from the previous milestone.}

\subsection{Functionality assessment}

Functionality requirements:
%
\begin{flushleft}
  \begin{tabular}{l|l}
    Wacky racer & Wacky hat \\ \hline \hline
    Blink LED                      & Blink LED \\
    Drive motors forward/backward  & Read from IMU \\
    Speed control of motors        & Calculate speeds from IMU \\
    Steering control               & Joystick control \\
    Receive radio message          & Send radio message \\
    Jumper selectable radio channel & Jumper selectable radio channel  \\    
    Dies on bump                   & Plays sound on bump \\
    Report group info to game server & Report group info to game server \\
    Low voltage indication         & Low voltage indication \\
  \end{tabular}
\end{flushleft}
%
Marks are allocated on how well things work.  Up to 5 bonus marks can
be awarded for extra functionality such as:
%
\begin{flushleft}
  \begin{tabular}{l|l}
    Wacky racer                & Wacky hat \\ \hline \hline
    Dastardly stuff            & Plays interesting sounds \\
    Sleep mode                 & Sleep mode \\
  \end{tabular}
\end{flushleft}

\subsection{Competition}

The competition is a race around an obstacle course.  Marks will be
awarded every time you pass over a Wacky Ramp in the correct order.
These ramps have an RFID card reader that will detect your Racer if
you have correctly fitted an RFID card.  The Wacky Ramps change colour
when they detect a Wacky Racer.

To be awarded any marks for the race:
%
\begin{enumerate}
\item Your vehicle must stop for at least 5\,s if the bumper is hit.

\item Your vehicle must be controlled by motions of the Wacky hat
  sitting on someone's head.
\end{enumerate}

\subsection{PCB inspection}

This is assessed after the competition.  The categories are:
%
\begin{enumerate}
\item Layout (component placement etc.)
\item Construction (tidiness, rework, etc.)
\item Testability  
\item Power supplies (routing, decoupling, etc.)
\end{enumerate}

\section{Technical stuff}

Read this section carefully.  There are clues as to how we mark your
PCBs at the end of the assignment.

\subsection{Version control}

Use version control for everything, or else!  Learning git is
frustrating but is a skill you will not regret.

Your group leader should create a forked copy of the wacky-racers-2020
git project and then add the other group members to the project.  This
can be done by:

\begin{enumerate}
\item Go to \url{https://eng-git.canterbury.ac.nz/wacky-racers/wacky-racers-2020}

\item Click `Fork' button.  This will create a copy of the main repository for the project.

\item Click on the `Settings' menu then click the `Expand' button for
`Sharing and permissions'.  Change `Project Visibility' to `Private'.

\item Click on the `Members' menu and add group members as Developers.

\item Using a bash terminal (or other useful shell), enter the command:

  \lstset{language=bash}
  \lstset{basicstyle=\ttfamily\small}
  \lstset{keywordstyle=\color{black}\ttfamily}
  \lstset{breaklines}
  
\begin{lstlisting}
  $ git clone https://eng-git.canterbury.ac.nz/your-userid/wacky-racers-2020.git wacky-racers
\end{lstlisting}

If you do not want to have to enter your password for every git
push/pull operation, you should set up ssh-keys and use:

\begin{lstlisting}[breaklines]
  $ git clone git@eng-git.canterbury.ac.nz:your-userid/wacky-racers-2020.git wacky-racers
\end{lstlisting}

\item Add a remote URL for the main repository.
%
\begin{lstlisting}[breaklines]
  $ cd wacky-racers 
  $ git remote add upstream https://eng-git.canterbury.ac.nz/wacky-racers/wacky-racers-2020.git  
\end{lstlisting}
%
Again if you do not want to manually enter your password, you can use:
%
\begin{lstlisting}[breaklines]
  $ cd wacky-racers 
  $ git remote add upstream git@eng-git.canterbury.ac.nz:wacky-racers/wacky-racers-2020.git    
\end{lstlisting}
%
If we add more demo code or tweak the instructions in the main
repository, you can get the updated stuff using:
%
\begin{lstlisting}[breaklines]
  $ git pull upstream master
\end{lstlisting}
\end{enumerate}

\subsection{Components}

\begin{enumerate}
\item We recommend that you use components in the ECE Altium library.
  These are stocked in the SMT lab.  For any other components you may
  require, see Scott Lloyd in the SMT lab.

\item The Wacky Racer batteries are Turnigy 5-cell 6\,V, 2300\,mAh,
  NiMH with a three pin JST connector.  To preserve the battery life
  it is imperative to not draw current when the battery voltage is
  below 5\,V.
\end{enumerate}

\subsection{Connectors}

\begin{enumerate}
\item USB micro or mini connector for debugging
\item 3 pin 0.1'' for LED tape (pin 1 5\,V, pin 2 signal, pin 3 ground)
\item 2 pin 0.1'' for bumper (pin 1 switch, pin 2 ground)
\item 10 pin IDE for serial wire debug  
\item 3 pin JST power connector (pin 1 GND, pin 2 VBAT, pin 3 GND)
\item motor connectors (for Racer)
\item connectors for dastardly stuff
\end{enumerate}

\subsection{Schematics}

\begin{enumerate}
\item Have a look at the
  \href{http://ecewiki.elec.canterbury.ac.nz/mediawiki/index.php/ENCE461_Altium_tutorial}{Altium
    tutorial on ecewiki}.

\item Have a read of the
  \href{http://ecewiki.elec.canterbury.ac.nz/mediawiki/index.php/Schematic_guidelines}{schematic
    guidelines on ecewiki}.

\item Add you and your partner's name and your group number to the
  title block on your schematic.

\item Save PDF files of your schematics in your source repository.
  \textbf{Note, when debugging your PCBs, we will not help you until
    you show us your printed A3 schematic}.

\item We bet that you will not have enough test points to clip an
  oscilloscope probe to.  Do not think you can hold the probe tip
  against an MCU pin.  Ensure you give a meaningful name to the test
  point.  A ground test point is essential for an oscilloscope earth
  clip. Keep this clear of other test points since the clip may short
  against them.  You will probably require at least two ground points.
  
\item Checking the schematic is the most crucial part of the
  assignment.  If the schematic is wrong then your PCB will be wrong.
  So, schematics must be thoroughly checked by another person.

\item Consider fall-back options if you have a problem with your PCB.

  The IMU for the Wacky Hat is tiny and we \textbf{strongly recommend} that you
  provide an alternative connector for connecting the following IMU module:
  \href{https://www.aliexpress.com/item/SPI-IIC-MPU9250-MPU-9250-MPU-9250-9-Axis-Attitude-Gyro-Accelerator-Magnetometer-Sensor-Module-MPU9250/32216818498.html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}{MPU-9250 on AliExpress}

  Similarly for the Wacky Racer, in case the H-bridge fails, provide two
  three-pin servo connectors so that external Electronic Speed
  Controllers (ESC) can be used to drive the motors.

\item It would be useful to have a jumper or two connected to a PIO
  pin so that you can configure your board.  For example, if a jumper
  is in, use the joystick, otherwise use the IMU.
  
\end{enumerate}

\subsection{PCBs}

\begin{enumerate}
\item Your four-layer PCBs are going to be manufactured in batches.
  There is at least a week turnaround time to get the boards made.

\item It is important that you check footprints for parts they you
  create.  We will impose a 10\% penalty for each rerun of a PCB, say
  due to a footprint mistake.  Get your partner to check.
  
\item PCB layouts must be thoroughly checked by another person.
  
\item A PCB track can blow faster than a fuse. So keep high current
  tracks fat and short.

\item Clearly mark the positive and negative battery connections on
  the silk screen.

\item Some of the chips can get hot so thermal considerations are
  required.  Follow the manufacturers' guidelines in the datasheets.

\item The switching regulators can interfere with the radios.
  
\item Use a design rule check to see if any of the following
  constraints are violated:
%
\begin{itemize}
\item Minimum trace width (0.15\,mm)
\item Minimum trace clearance (0.15\,mm)
\item Minimum via size (0.3\,mm hole, 0.6\,mm outer diameter)
\item Minimum hole size (0.3\,mm)
\item Minimum annular ring (0.1\,mm)
\end{itemize}
%
For every violation of one these rules, we will deduct 1\% from your
final mark.

\item Check the
  \href{http://ecewiki.elec.canterbury.ac.nz/mediawiki/index.php/PCB_checklist}{PCB
    checklist on ecewiki} before submission.
\end{enumerate}

\subsection{Assembly}

\begin{enumerate}
\item Finding shorts is extremely frustrating so maximise clearances
  and test for shorts before populating components.

\item Components can be put through the oven on the reverse side
  although heavy components may need to be glued.
  
\item Never assume where pin 1 is on an IC; check the datasheet.
  5--10\% of groups will get this wrong.
  
\end{enumerate}

\subsection{Software}

\begin{enumerate}
\item We highly recommend using a personal laptop with Linux installed if
possible. A virtual machine running on Windows is acceptable for this. You will
need to check instructions on ecewiki for how to install the required toolchain.

\item We do not support embedded systems development on Windows, but
  it is possible.

\item If you are not using version control for this you are foolish.

\item Inspect MPH's sample code.

\end{enumerate}

\subsection{Programming}

\begin{enumerate}
\item If you are trying to program the SAM4S for the first time and
  are feeling tired or impatient, then do something else.

\item For the first program, do not use batteries or a USB connection.
  The ST-Link adapter will provide 3.3\,V to the MCU.
 
\item Detailed instructions can be found at
  \url{http://ecewiki.elec.canterbury.ac.nz/mediawiki/index.php/Wacky_racers_software}.
\end{enumerate}

\subsection{Debugging}

\begin{enumerate}
\item Start running small programs (such as the provided demo
  programs) to test each feature separately.
  
\item An oscilloscope is your friend.

\item It is possible to use the GDB debugger but you need to know what
  you are doing, especially with optimised code.

\item Drawing a diagram of what you think is happening is highly recommended. A
simple circuit diagram or timing diagram will often help you realise what you
have missed and let you fix it without asking for help.
  
\end{enumerate}

\subsection{Possibly asked questions with answers}

\begin{itemize}
\item \emph{Why use the SAM4s MCU?}  For this application most MCUs
  would suffice, even an 8-bit AVR microcontroller.  To level the
  playing field, I have chosen a MCU most students would not have used
  before.  This is an ARM based MCU made by Atmel I have used this in
  a number of projects.  Indeed we used to teach this chip in ENCE361.
  There are many other similar MCUs made by different manufacturers
  such as the STM32 that would just as suitable.

\item \emph{Why use a four layer PCB?}  Come to lectures to find out!

\item \emph{Why use 7.2\,V NiMH batteries for the Wacky Racers?}
  These were a legacy of previous Wacky Racers.  They are also safer
  than lithium batteries with sleep-deprived students.

%% \item \emph{Why can't I program my device using Windows?} Due to
%%   various aspects of the Windows ecosystem, setting up a fully
%%   functional build environment is more complicated, will often vary
%%   from machine to machine, will often break filepaths, and will often
%%   cause bizarre compilation errors. Use at your own risk, we will not
%%   assist in debugging issues related to Windows.

\end{itemize}

\section{Assistance}

\begin{itemize}
\item Emails to the lecturers (except of a personal nature) will be
  quietly ignored.

\item Questions anwered on the ENCE461 Learn discussion page will be
  promptly answered.

\item All decisions regarding legality of your dastardly devices are
  at the whim of Ben Mitchell.  You can email Ben at
  \href{mailto://ben.mitchell@pg.canterbury.ac.nz}{ben.mitchell@pg.canterbury.ac.nz} if you wish to keep your ideas secret.

\item TAs will be available in the scheduled lab times.  Priority will
  be given to groups assigned to the current lab session.  We will
  only provide assistance to students who have a printed A3 schematic
  sheet in front of them and have already tried looking up the problem
  on \url{https://ecewiki.elec.canterbury.ac.nz}.

\item Questions pertaining to Altium and surface mount rework will be
  answered by Scott Lloyd (SMT Lab technician) and Diego Ramirez
  (Electronics Lab technician).

\item Michael Hayes is really busy pulling all the string behind the
  scenes and so will only help with gnarly problems referred to by the
  TAs!
  
\end{itemize}

\end{document}

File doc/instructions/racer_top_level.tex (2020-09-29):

\begin{tikzpicture}[scale=0.9]
    
    \draw[black, very thick, fill=blue!50] (-2, -1) rectangle (2, 1);
    \node at (0, 0) {SAM4S};

    % H-bridge
    \draw[black, very thick] (4, -1) rectangle (7, 1);
    \node at (5, 0) {H-bridge};
    \draw[-triangle 45] (2, 0) -- (4, 0);
    \draw[black, thick] (6, 0.8) rectangle (7, 0.2);
    \node at (6.5, 0.5) {M1};
    \draw[black, thick] (6, -0.8) rectangle (7, -0.2);
    \node at (6.5, -0.5) {M2};

    % Dastardly
    \draw[black, very thick] (4, -2) rectangle (7, -4);
    \node at (5.5, -3) {Dastardly stuff};
    \draw[-triangle 45] (2, -1) -- (4, -2);

    % LED tape
    \draw[black, very thick] (-2, 2) rectangle (2, 4);
    \node at (0, 3) {LED tape};
    \draw[triangle 45-triangle 45] (0, 1) -- (0, 2);

    % Radio
    \draw[black, very thick] (-2, -2) rectangle (2, -4);
    \node at (0, -3) {Radio};
    \draw[triangle 45-triangle 45] (0, -1) -- (0, -2);
    \draw (0.354, -4.354) arc (-45:-135:0.5);
    \draw (0.707, -4.707) arc (-45:-135:1);
    \draw (1.061, -5.061) arc (-45:-135:1.5);

    % Power
    \draw[black, very thick] (-4, 2) rectangle (-7, 4);
    \node at (-5.5, 3) {Power};
    \draw (-5, 2) -- (-5.25, 1.4) -- (-4.75, 1.6) -- (-5, 1);
    \draw (-6, 2) -- (-6.25, 1.4) -- (-5.75, 1.6) -- (-6, 1);
    
    % USB
    \draw[black, very thick] (-4, -2) rectangle (-7, -4);
    \node at (-5.5, -3) {USB};
    \draw[triangle 45-triangle 45] (-2, -1) -- (-4, -2);

\end{tikzpicture}

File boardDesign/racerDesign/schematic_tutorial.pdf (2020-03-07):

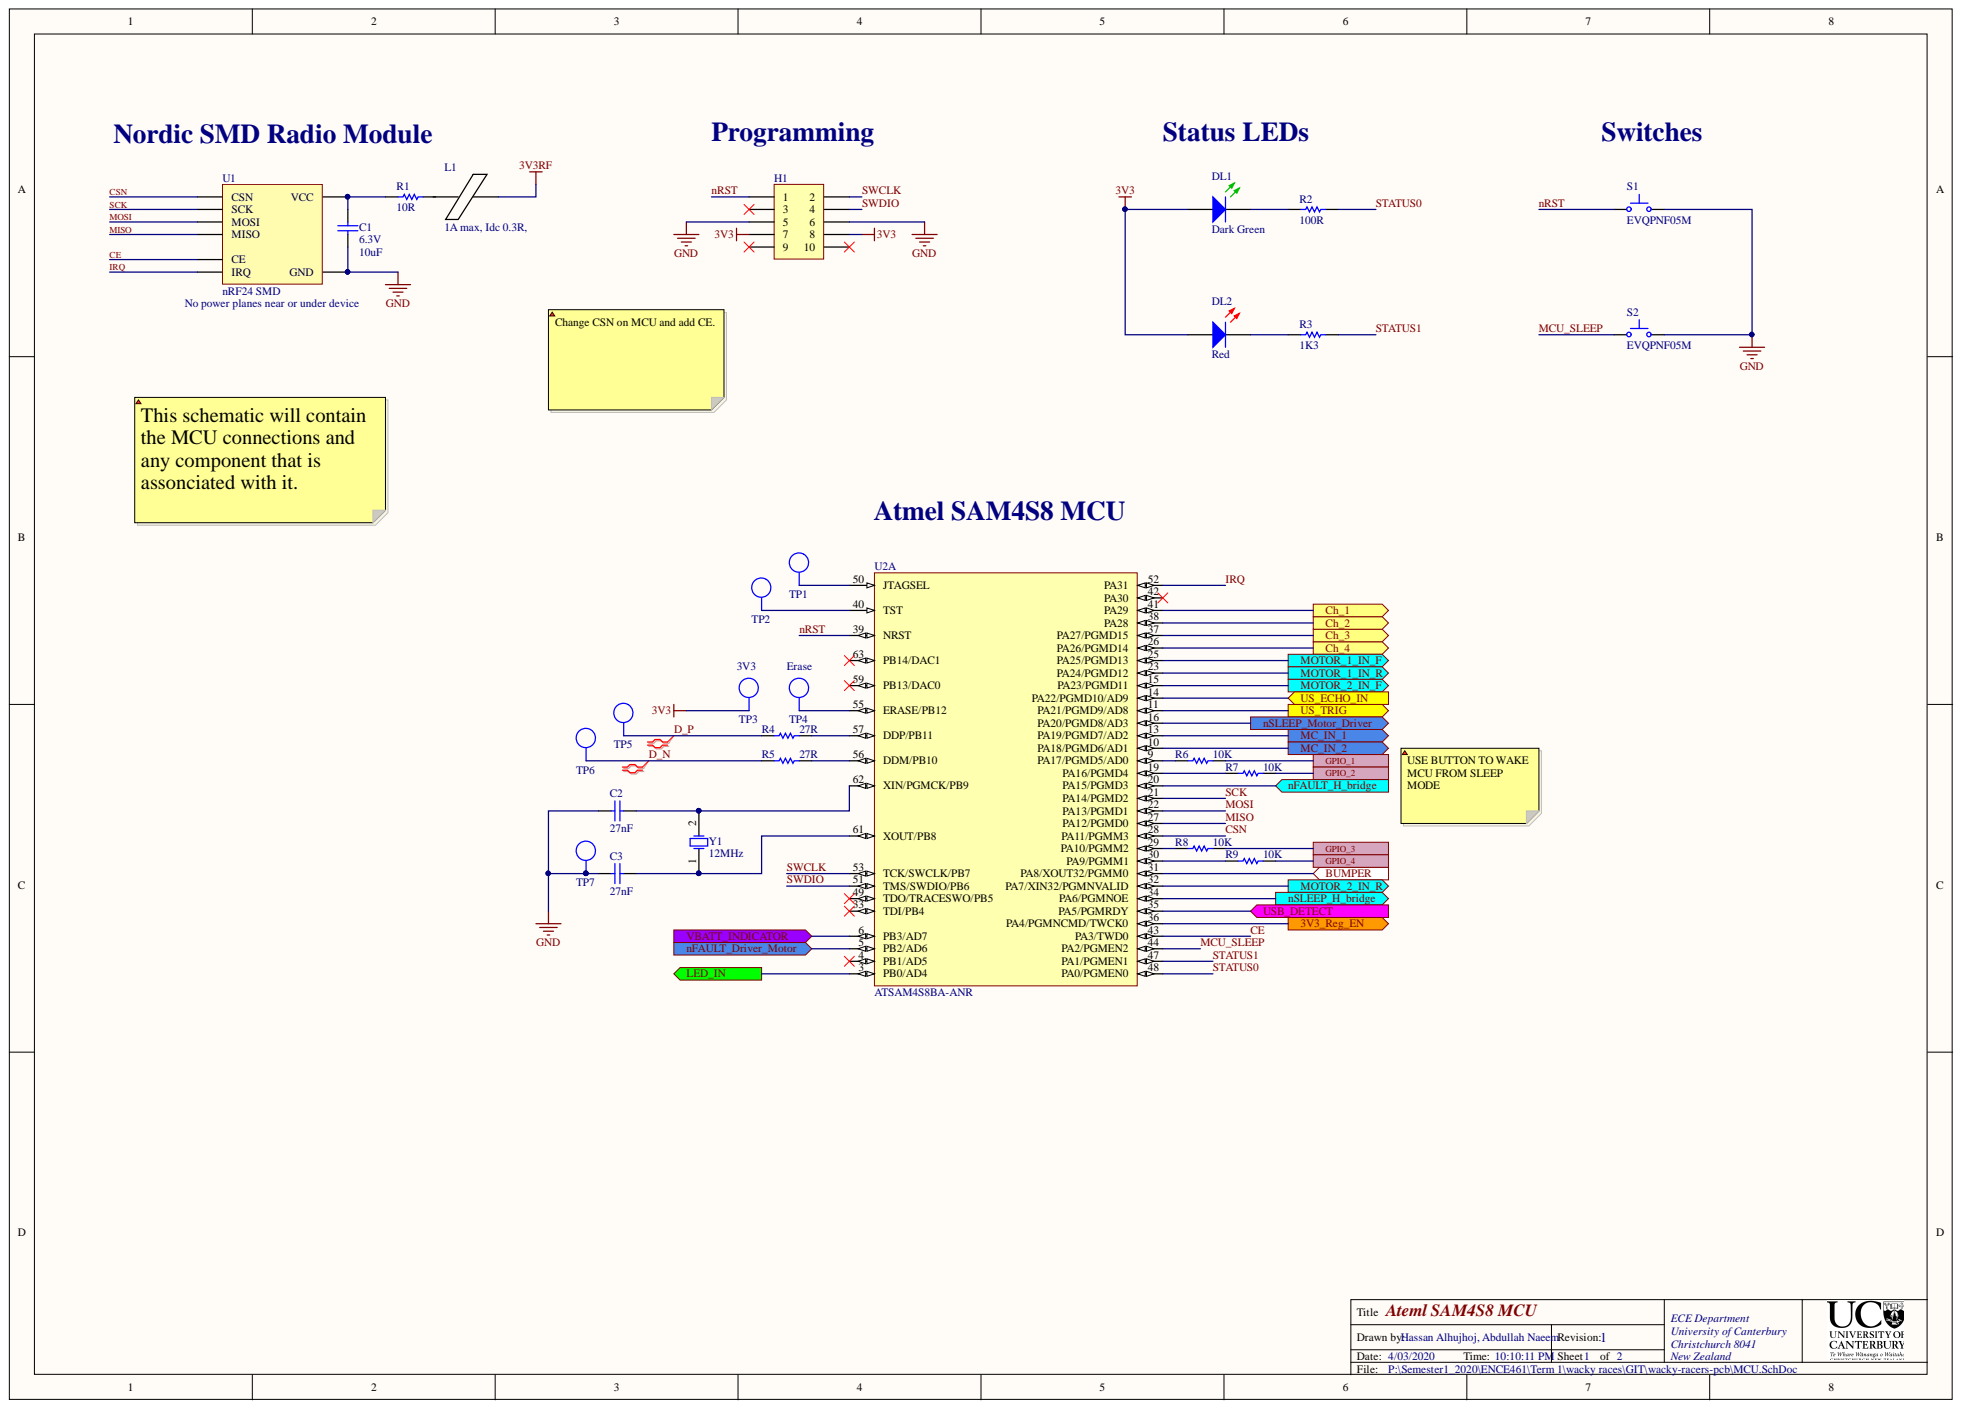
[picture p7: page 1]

Nordic SMD Radio Module

No power planes near or under device

Change CSN on MCU and add CE.

This schematic will contain
the MCU connections and
any component that is
assonciated with it.

USE BUTTON TO WAKE
MCU FROM SLEEP
MODE

Y1 | R8 10K | GPIO_3

Ateml SAM4S8 MCU Title | ECE Department University of Canterbury Christchurch 8041 New Zealand

Drawn by: Hassan Alhujhoj, Abdullah Naeem | Revision:
Date: 4/03/2020 Time: 10:10:11 PM | Sheet of 2

P:\Semester1_2020\ENCE461\Term 1\wacky races\GIT\wacky-racers-pcb\MCU.SchDoc

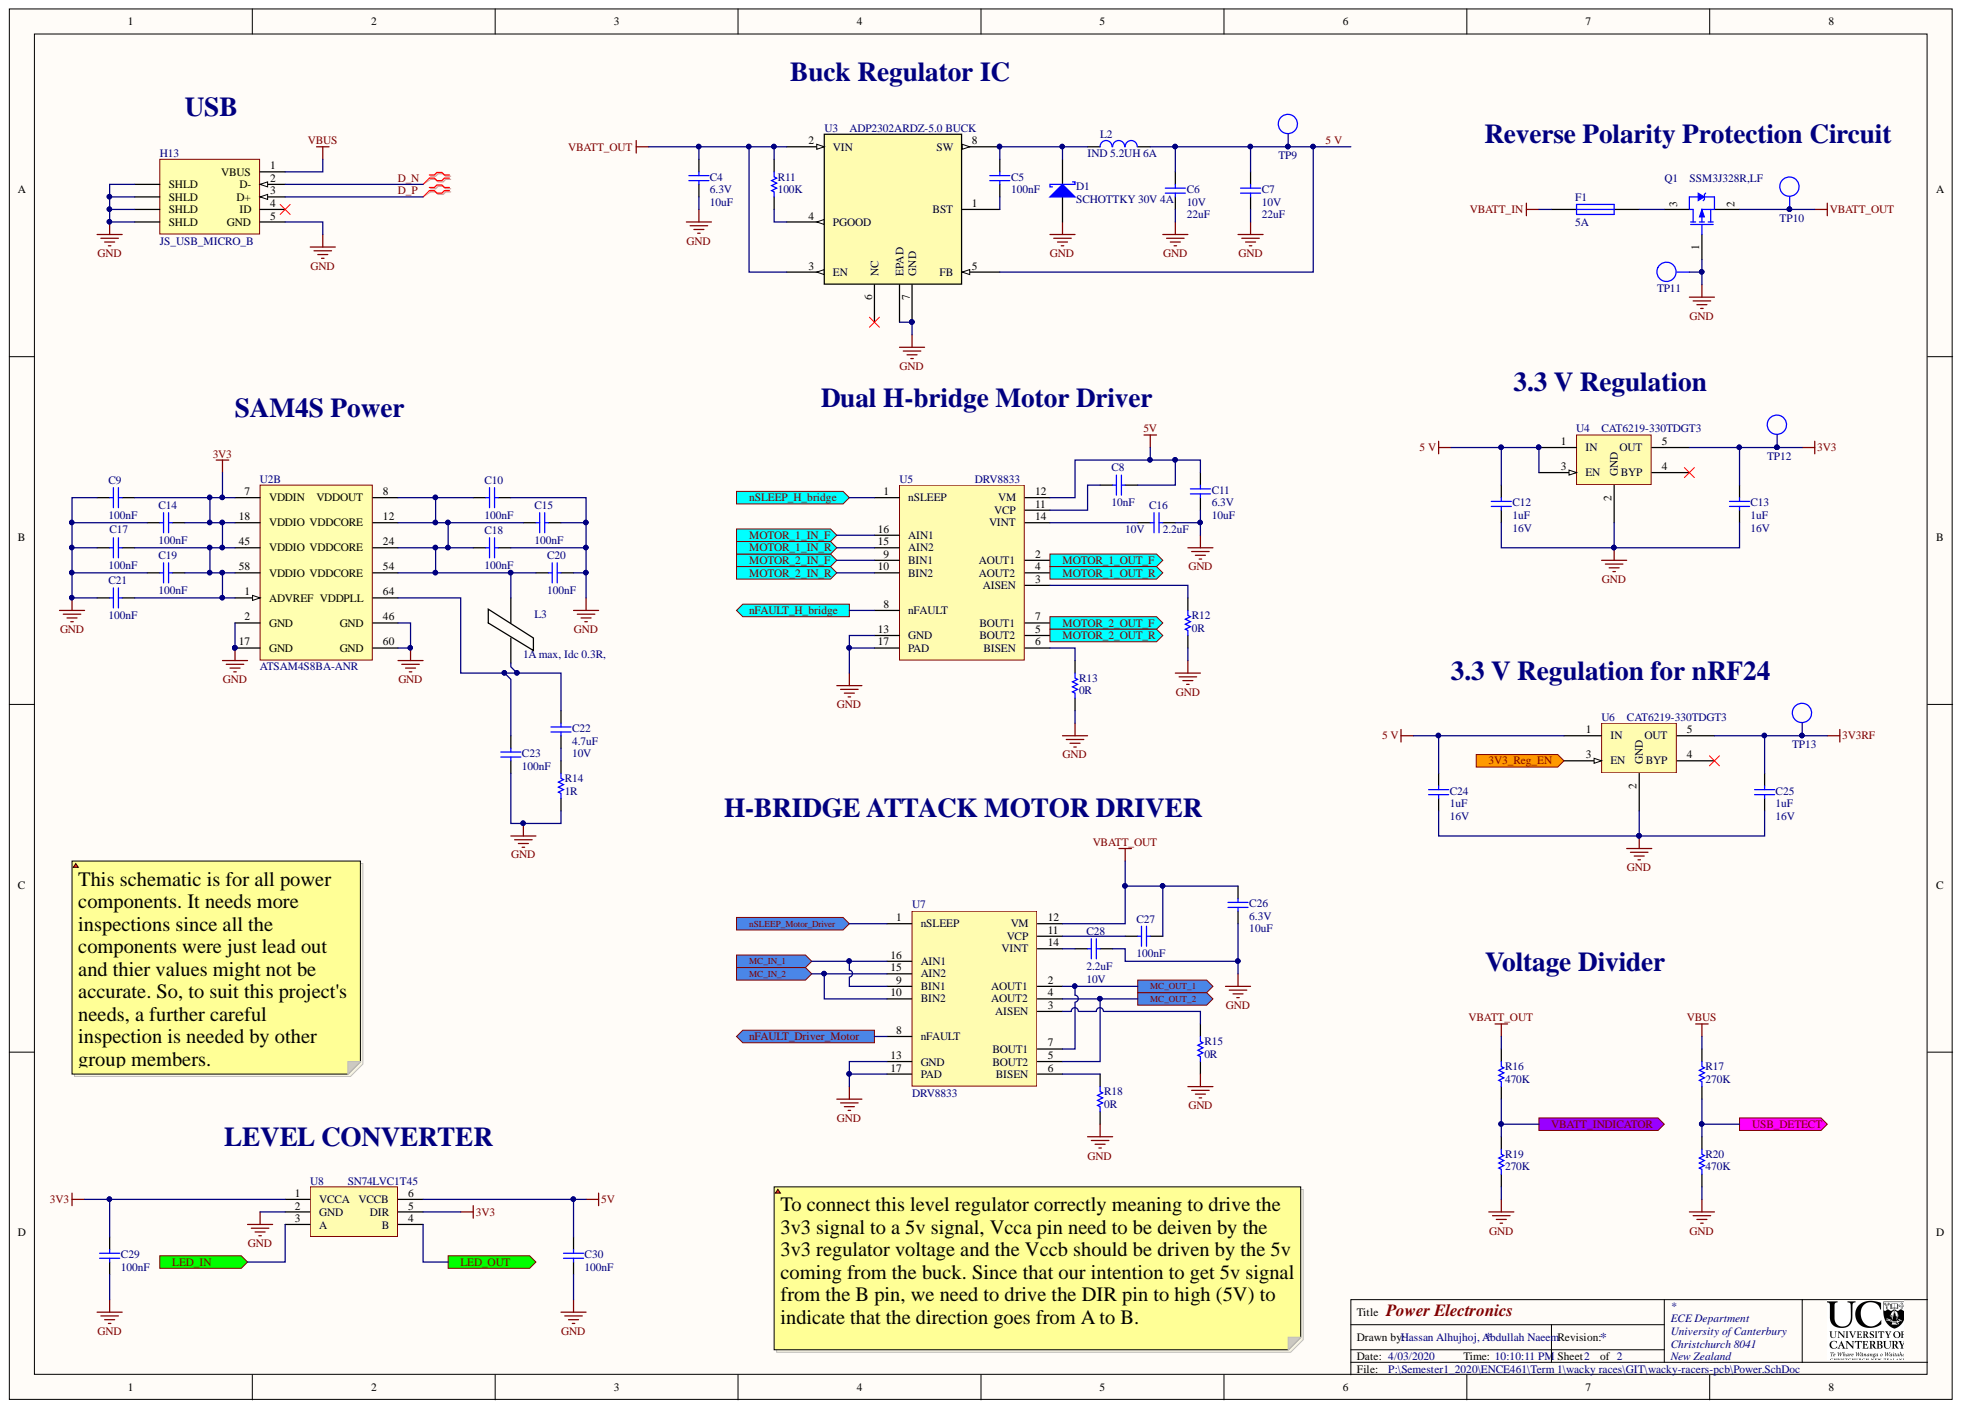
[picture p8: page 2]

Reverse Polarity Protection Circuit

Dual H-bridge Motor Driver

H-BRIDGE ATTACK MOTOR DRIVER

This schematic is for all power
components. It needs more
inspections since all the
components were just lead out
and thier values might not be
accurate. So, to suit this project's
needs, a further careful
inspection is needed by other
group members.

To connect this level regulator correctly meaning to drive the
3v3 signal to a 5v signal, Vcca pin need to be deiven by the
3v3 regulator voltage and the Vccb should be driven by the 5v
coming from the buck. Since that our intention to get 5v signal
from the B pin, we need to drive the DIR pin to high (5V) to
indicate that the direction goes from A to B.

Power Electronics | * New Zealand

P:\Semester1_2020\ENCE461\Term 1\wacky races\GIT\wacky-racers-pcb\Power.SchDoc

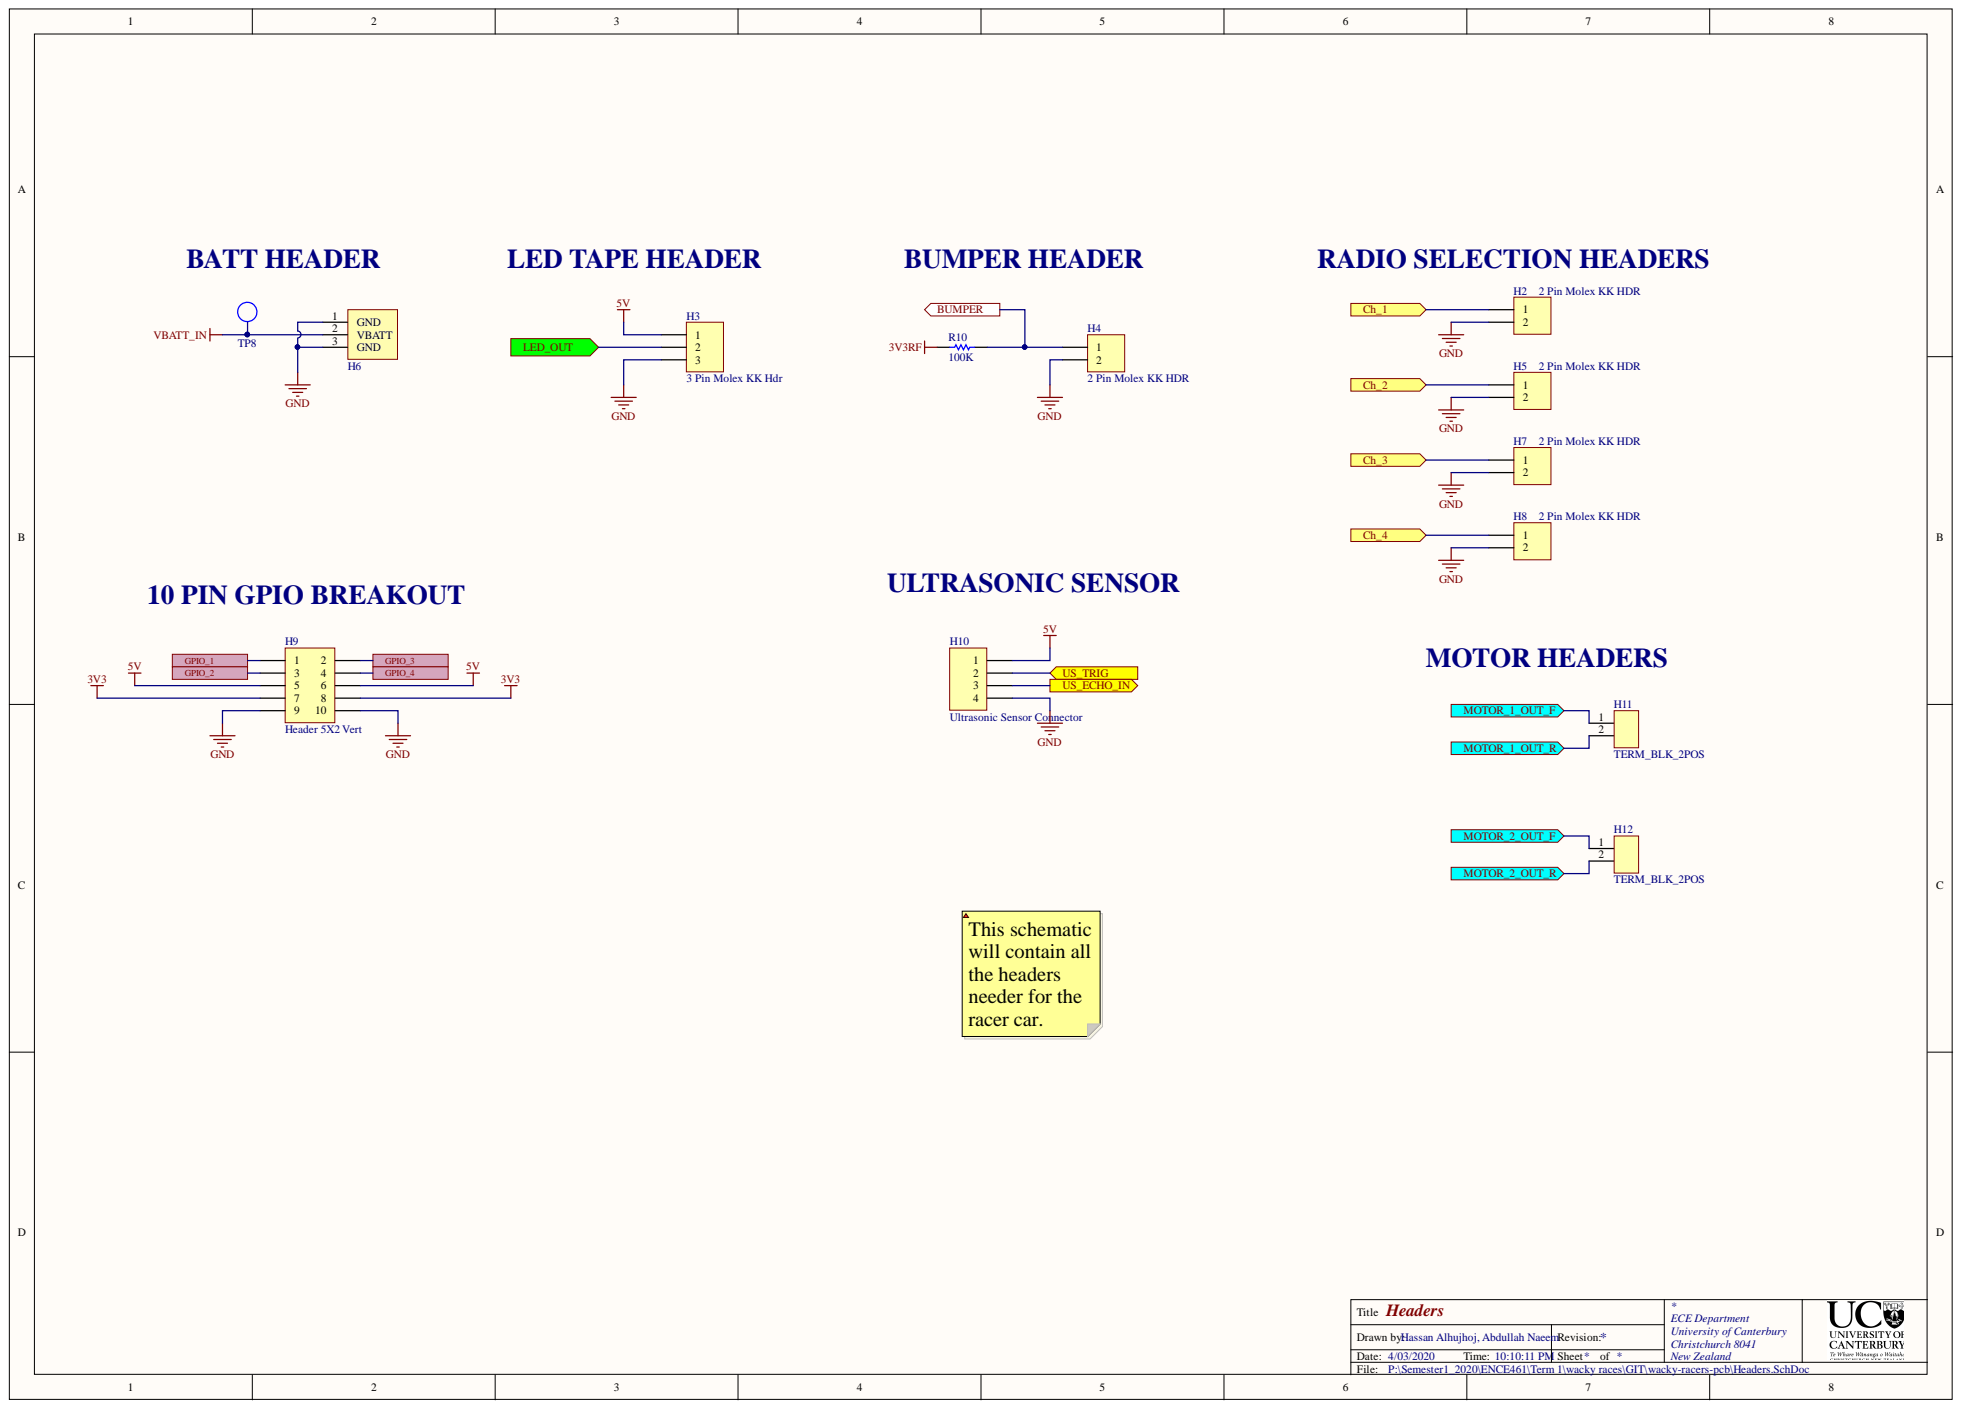
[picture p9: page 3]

Headers | * New Zealand

* *

P:\Semester1_2020\ENCE461\Term 1\wacky races\GIT\wacky-racers-pcb\Headers.SchDoc

Comment | Description | Designator | Footprint | LibRef | Quantity
10uF | CAP CER 10UF X5R +-20% C1, C4,C 11, C26 | | CAPC1608L | CC_10uF_0603 | 4
27nF | CAP CER 27nF X7R +-10% C2, C3 | | CAPC1608L | CC_27nF_0603 | 2
100nF | CAP CER 100nF X7R +-10% C5, C9,C10, C14, C15,CA PC1608 L | | | C_100n F_060 3 | 14
22uF | CAP CER 22uF Y5V -20%C6, C7 | | CAPC3216L | CC_22uF_1206 | 2
10nF | CAP CER 10nF X7R +-10% C8 | | CAPC1608L | CC_10nF_0603 | 1
1uF | CAP CER 1uF Y5V -20%C12, C13,C24, C25 | | CAPC1608L | CC_1uF_0603 | 4
2.2uF | CAP CER 2.2uF X5R +-20% C16, C 28 | | CAPC1608L | CC_2.2uF_0603 | 2
4.7uF | CAP CER 4.7uF X5R +-20% C22 | | CAPC1608N | CC_4.7uF_0603 | 1
SCHOTTKY 30V 4A | DIODE SCHOTTKY 30VD1 | | SMC | MBRS330T3G | 1
Dark Green | LED Dk Green 430mcd D L1 | | WL-SMCW0603 | DL_150060GS75000 | 1
Red | LED Red 250mcd 0603 DL2 | | WL-SMCW0603 | DL_150060RS75000 | 1
5A | Fuse 5.0A Fast Acting F 1 | | RESC3216N | FS_Fuse_5.0A | 1
Header 5X2 Vert | IDC Header, 2,54mm,H 1, H9 | | IDC2.54-V10D | JA_HDR_IDC_5X2_VE | 2
2 Pin Molex KK HDR | CONN HEADER 2POS | H2, H4, H5,H7,H8 | MOLEX_KK_2_HDR | JA_MOLEX_KK_2POS | 5
3 Pin Molex KK Hdr | CONN HEADER 3POS | H3 | MOLEX_KK_3_HDR | JA_MOLEX_KK_3POS | 1
Battery_HEADER_3pin3Pin Header 2.54mm spaH6 | | | BATT_HEADER_3POS | Battery_HEADER_3pin | 1
Ultrasonic Sensor ConCONN HEADER 4POS | | H10 | MOLEX_KK_4_HDR | JA_MOLEX_KK_4POS | 1
TERM_BLK_2POS | 2 Position Terminal BlockH11, H12 | | TERM_BLK_2POS | TERM_BLK_2POS | 2
JS_USB_MICRO_B | CONN USB MICRO B RH13 | | FCI_USB_10118194-0001L JS_USB_MICRO_B_SM | | 1
1A max, Idc 0.3R, | Ferrite Bead, Rdc 0.3RL1, L3 | | IN DC3216L | IN_Ferrite-Bead | 2
IND 5.2UH 6A | FIXED IND 5.2UH 6A 22 L2 | | INDUCTOR5u2 | CDRH104RNP-5R2NC | 1
SSM3J328R,LF | MOSFET P-CH 20V 6A Q1 | | SOT23_L | TM_SSM3J328R | 1
10R | RES 10 OHM 1/10W 5%R1 | | RESC1608L | RS_10R | 1
100R | RES 100 OHM 1/10W 5%R2 | | RESC1608L | RS_100R | 1
1K3 | RES 1.3K OHM 1/10W R3 | | RESC1608L | RS_1K3 | 1
27R | RES 27 OHM 1/10W 5%R4, R5 | | RESC1608L | RS_27R | 2
10K | RES 10.0K OHM 1/10W R6, R7, R8,R9 | | RESC1608L | RS_10K | 4
100K | RES 100K OHM 1/10W R10, R11 | | RESC1608L | RS_100K | 2
0R | RES 0.0 OHM 1/10W 5%R12, R13,R15 | | RESC1608L | RS_0R0 | 3
1R | RES 1R OHM 1/4W 5%R4 | | RESC3216L | RT_1R | 1
470K | RES 27 OHM 1/10W 5%R16, R20 | | RESC1608L | RS_27R, RS_47R | 2
270K | RES 27 OHM 1/10W 5%R17, R19 | | RESC1608L | RS_27R, RS_47R | 2
0R | RES 0R OHM 1/8W 5%R8 | | RESC3216L | RT_0R | 1
EVQPNF05M | Panasonic 6 x 3.5mm SS1,S2 | | EVQPNF05M | WS_EVQPNF05M | 2
TP_0603 | Test Point 1.65X0.9X1.TP8,TP9, TP12, TP13TP_0603 | | | TP_0603 | 4
nRF24 SMD | nRF24 SMD Module | U1 | NRF24 | NRF24 | 1
ATSAM4S8BA-ANR | IC MCU 32BIT 512KB FU2 | | LQFP64_L | SE_ATSAM4S16BA-MU | 1
ADP2302ARDZ-5.0 BUICREG BUCK 5V 2A 8SU3 | | | RD_8_1 | ADP2302ARDZ-5.0-R7 | 1
CAT6219-330TDGT3 | IC REG LIN 3.3V 500MU4,U6 | | SOT95P280X145-5N | SV_CAT6219-330TDGT | 2
DRV8833 | Dual H-Bridge Motor DU5, U7 | | HTSOP16 | DRV8833 | 2
SN74LVC1T45 | 1.8V - 5V level convertU8 | | SOT23-6_N | SN74LVC1T45 | 1
12MHz | Crystal Oscillator | Y1 | R38 | XTAL | 1

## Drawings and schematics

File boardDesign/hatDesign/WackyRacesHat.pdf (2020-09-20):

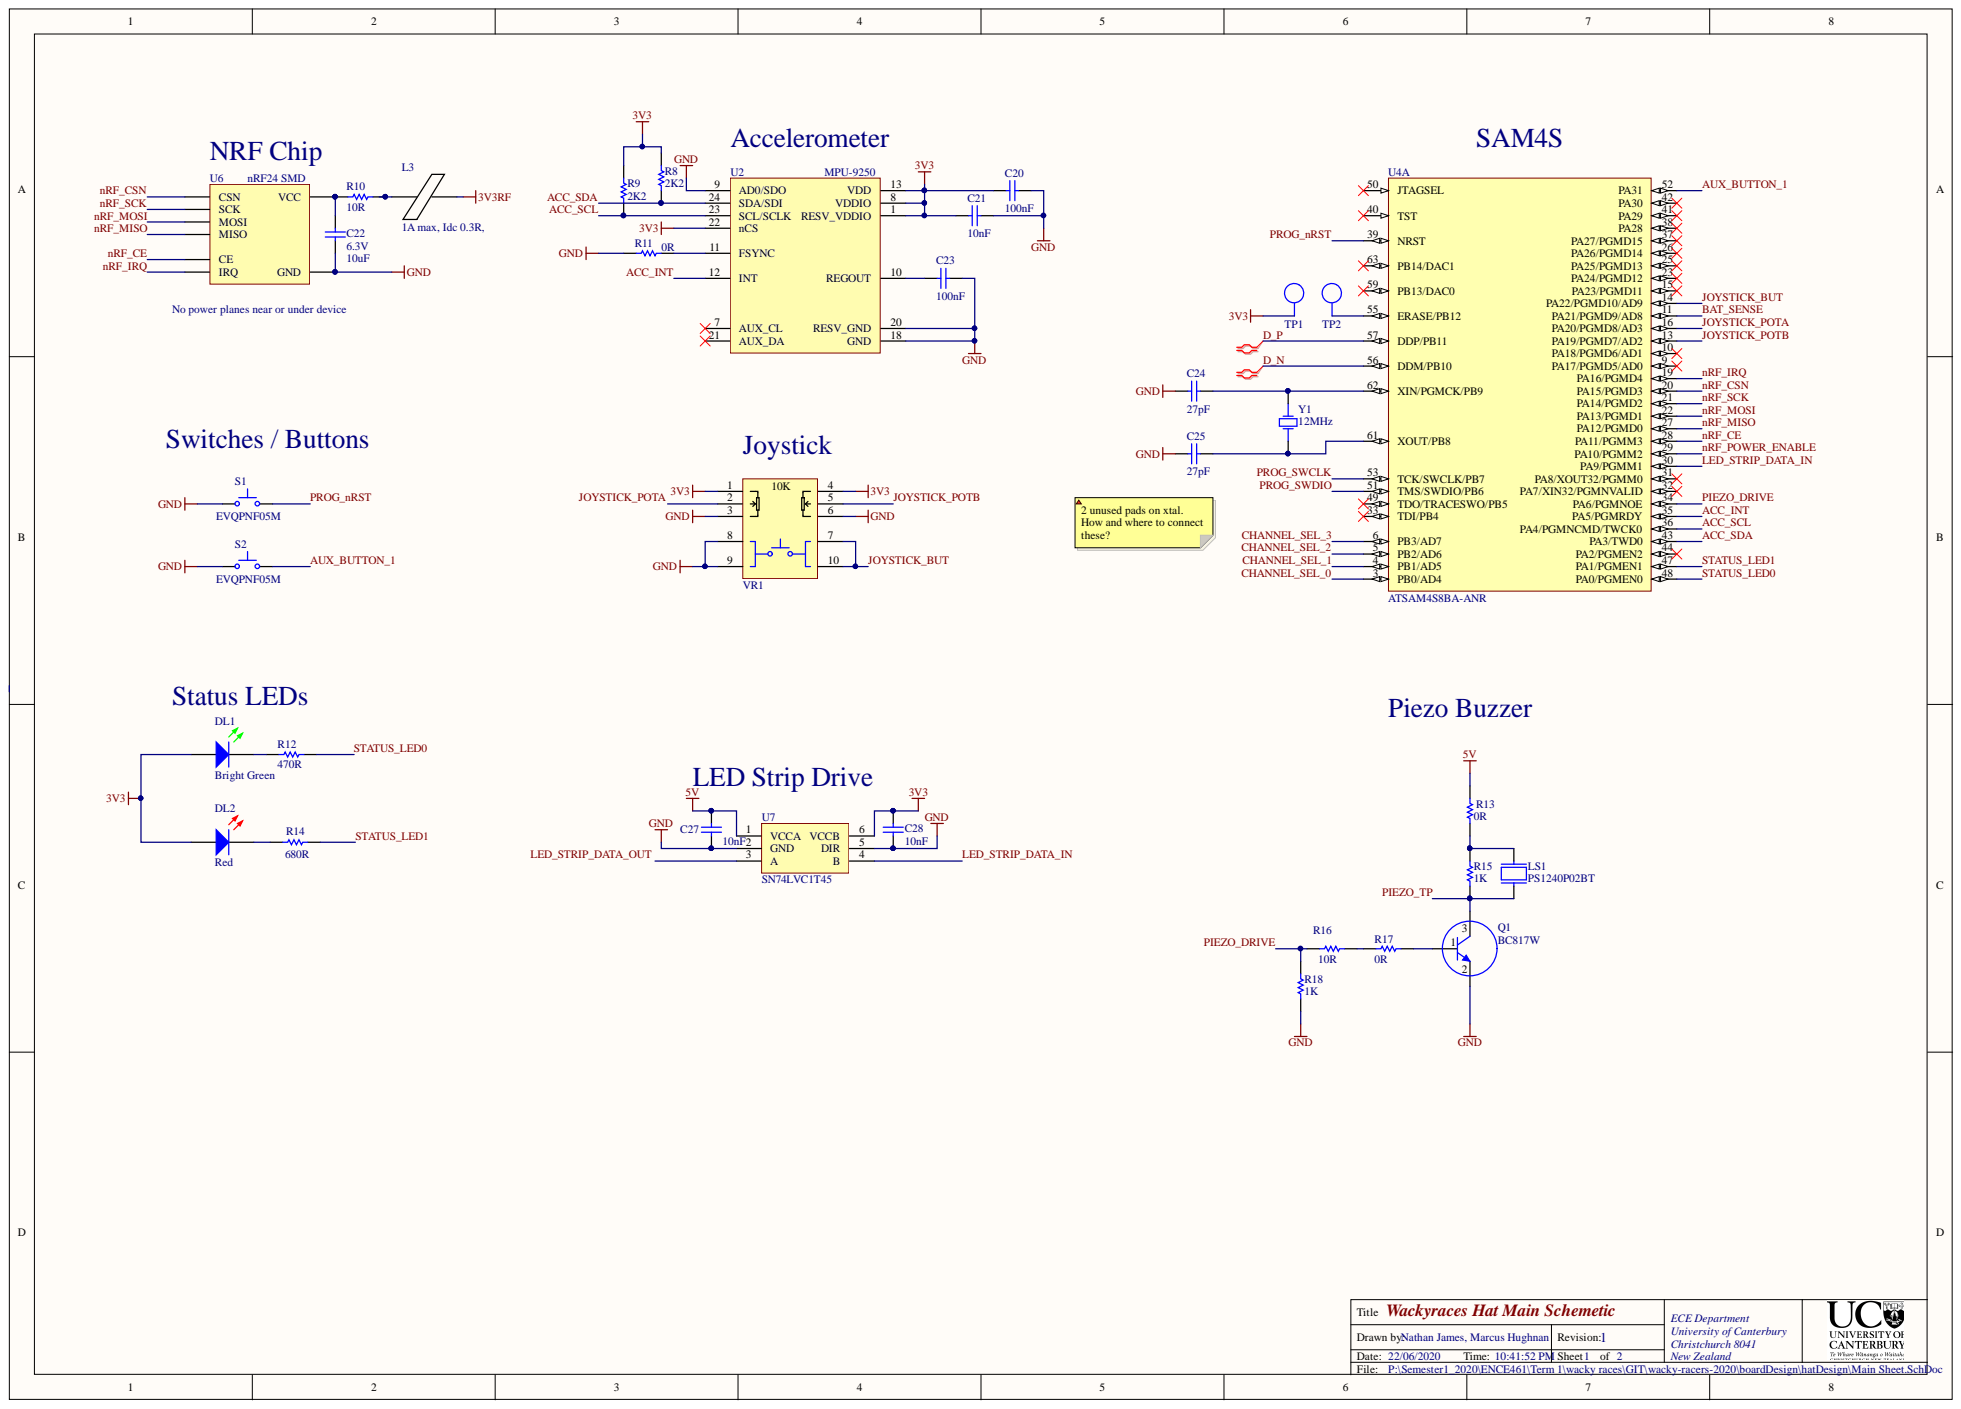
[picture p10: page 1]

No power planes near or under device

2 unused pads on xtal.
How and where to connect
these?

Wackyraces Hat Main Schemetic Title | ECE Department University of Canterbury Christchurch 8041 New Zealand

Drawn by: Nathan James, Marcus Hughnan | Revision:
Date: 22/06/2020 Time: 10:41:52 PM | Sheet of 2

P:\Semester1_2020\ENCE461\Term 1\wacky races\GIT\wacky-racers-2020\boardDesign\hatDesign\Main Sheet.SchDoc

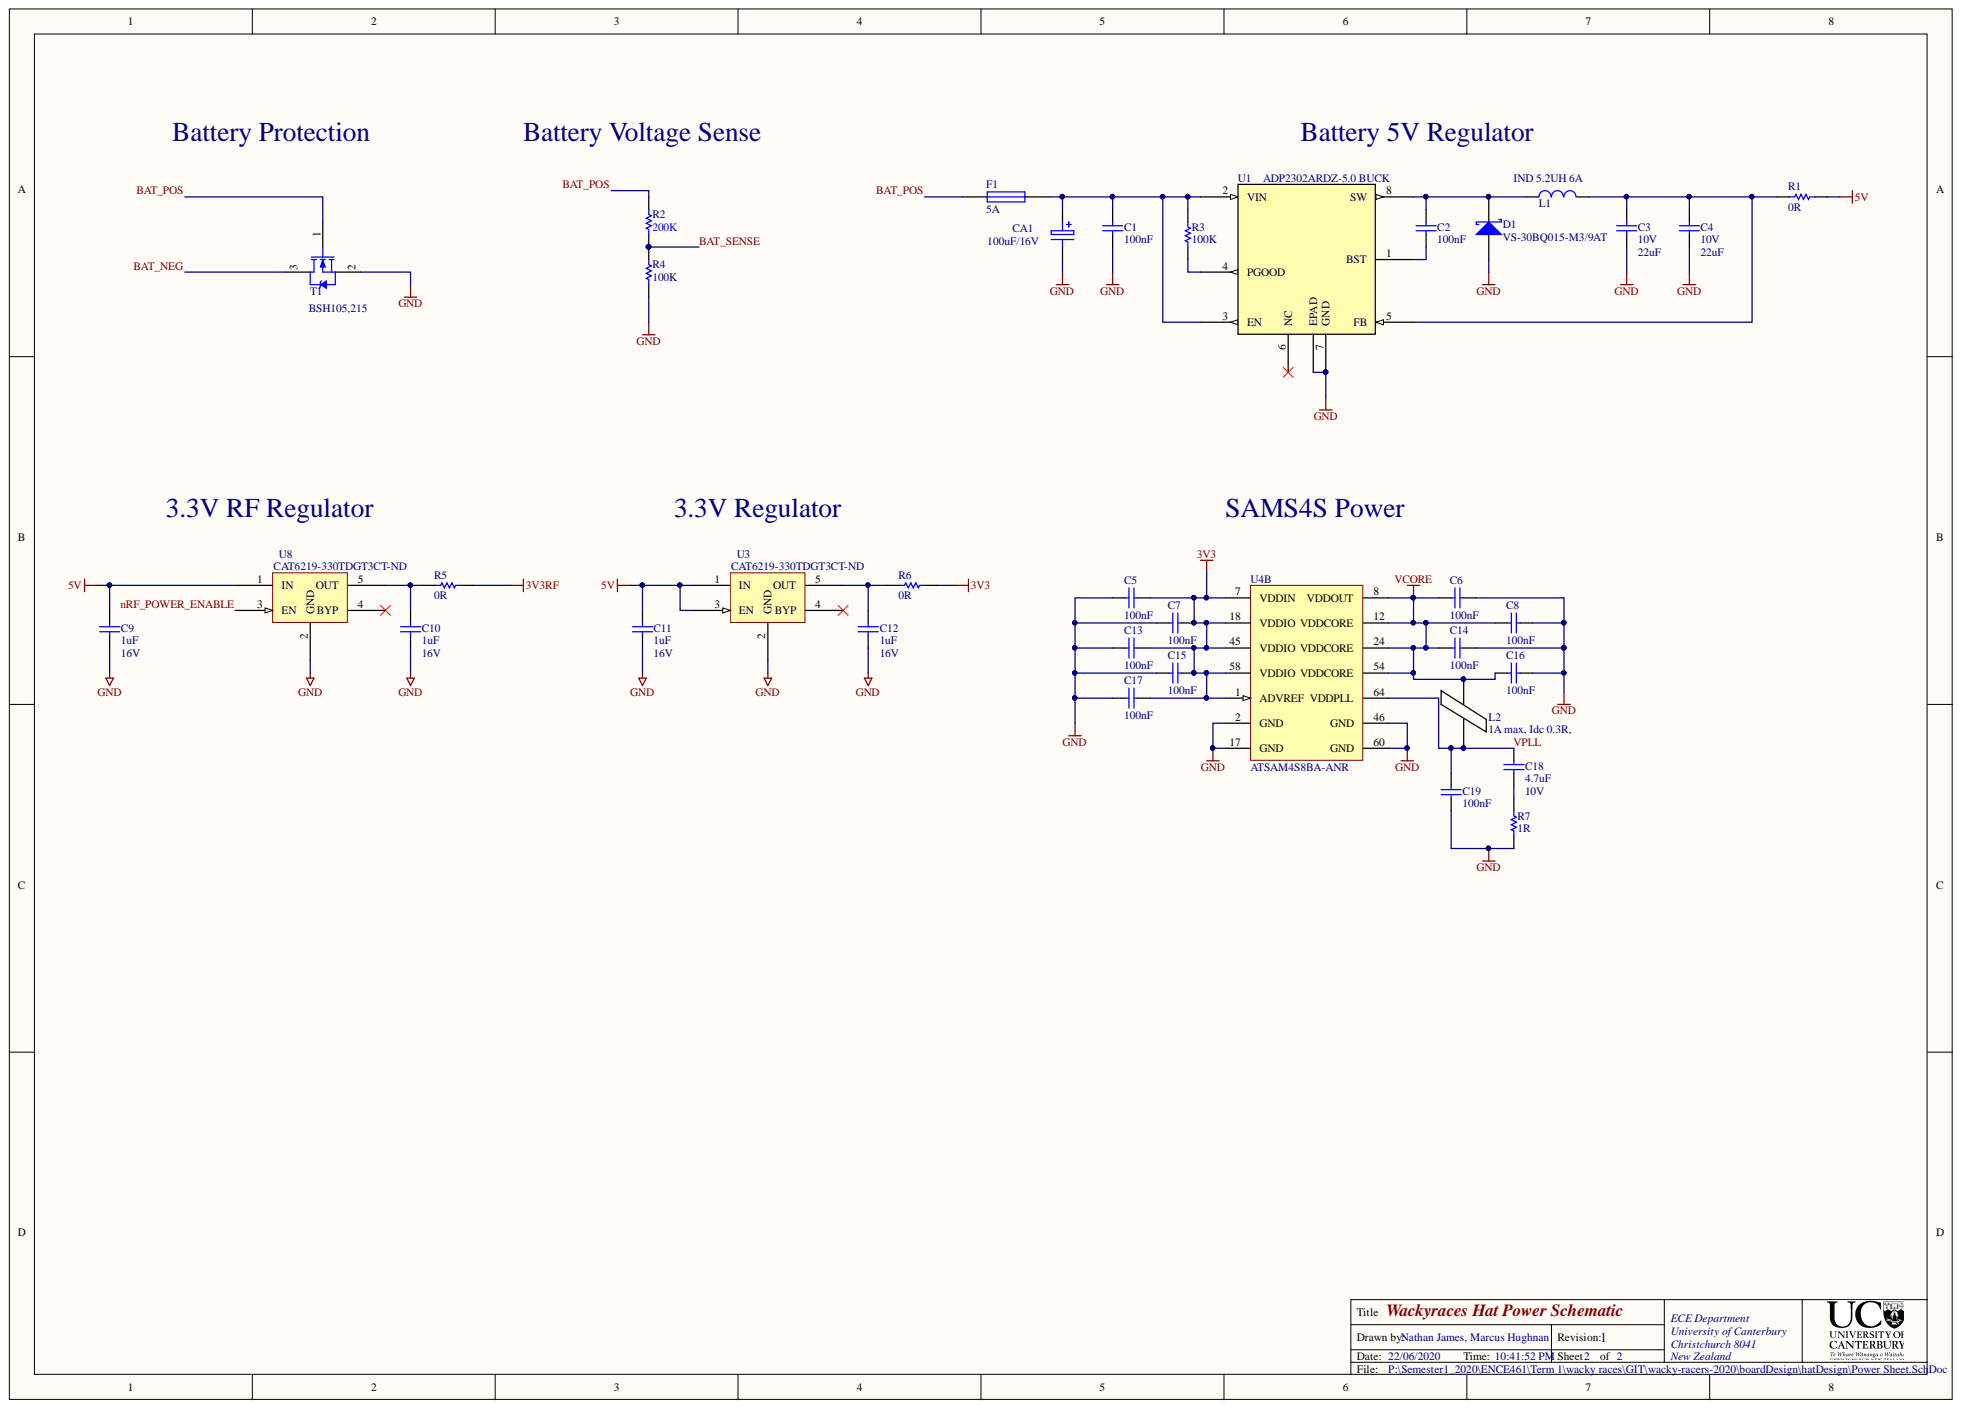
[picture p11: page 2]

VDDIO 58

GND 2

Wackyraces Hat Power Schematic | ECE Department University of Canterbury Christchurch 8041 New Zealand

Nathan James, Marcus Hughnan

P:\Semester1_2020\ENCE461\Term 1\wacky races\GIT\wacky-racers-2020\boardDesign\hatDesign\Power Sheet.SchDoc

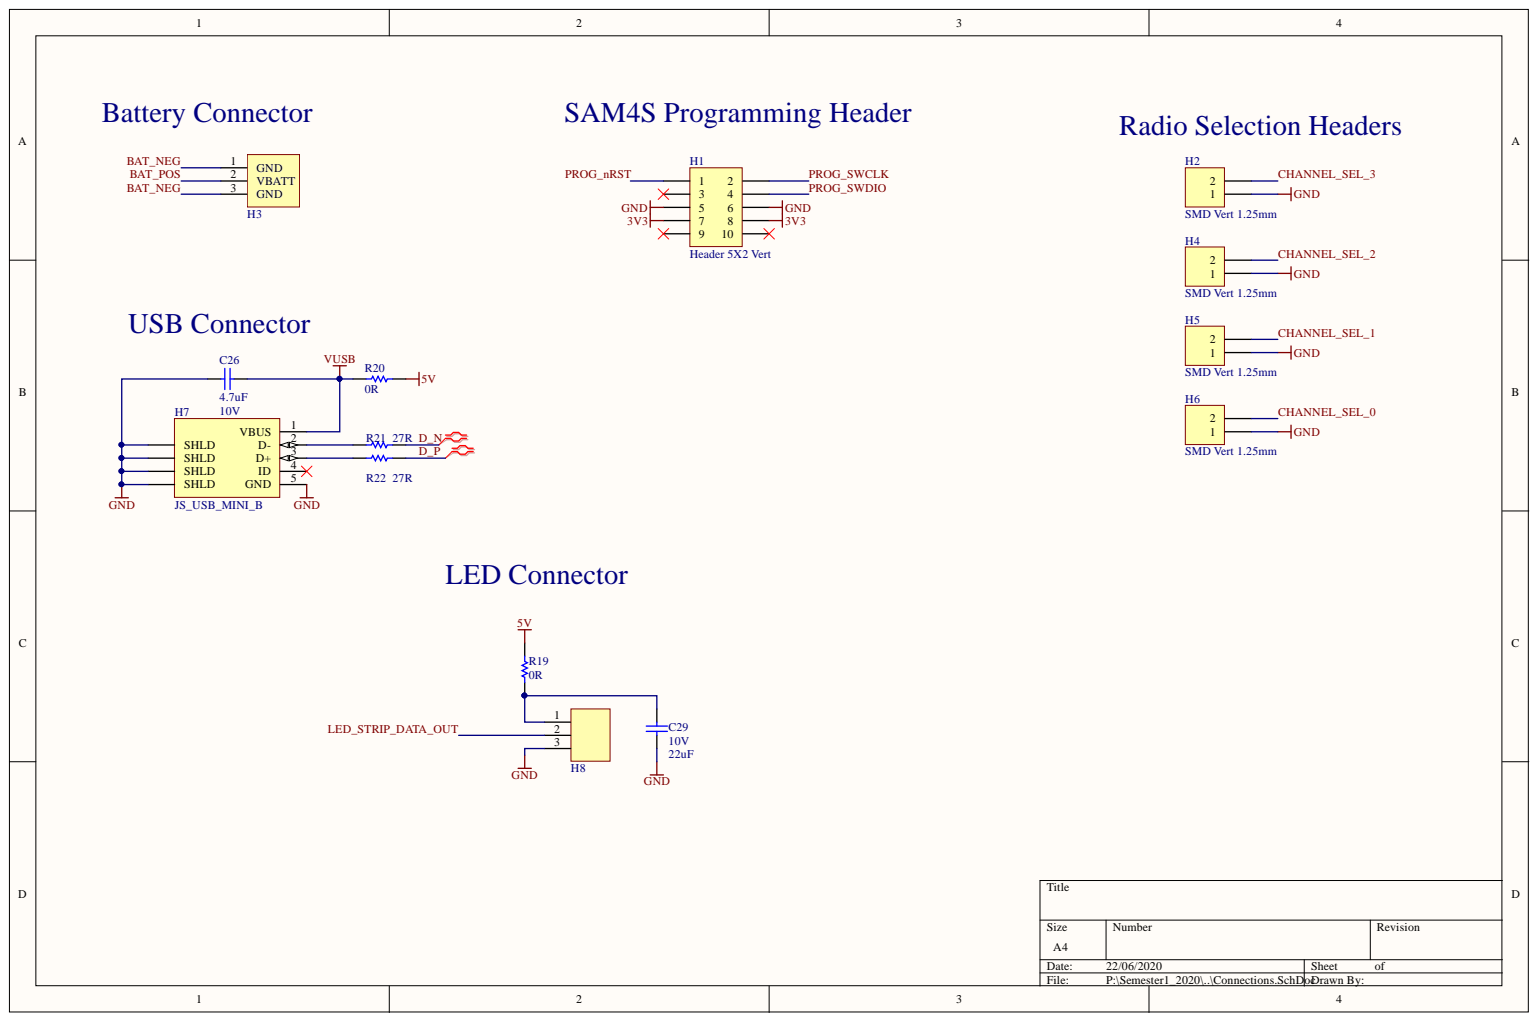
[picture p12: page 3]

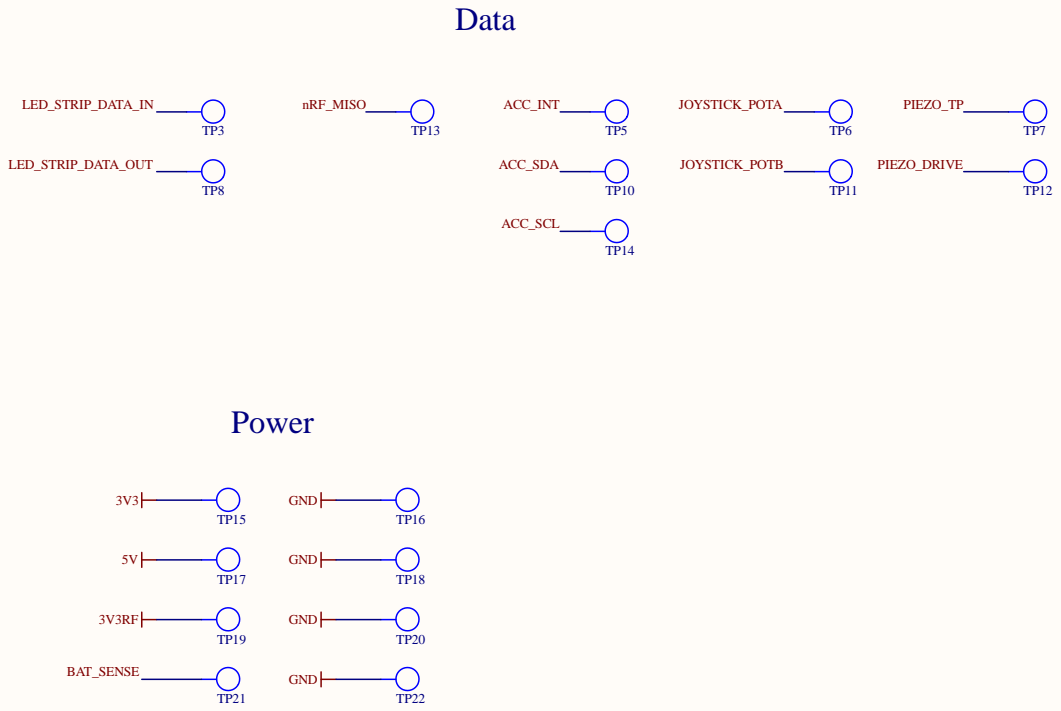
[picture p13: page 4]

P:\Semester1_2020\ENCE461\Term 1\wacky races\GIT\wacky-racers-2020\boardDesign\hatDesign\Test Points Sheet.SchDoc

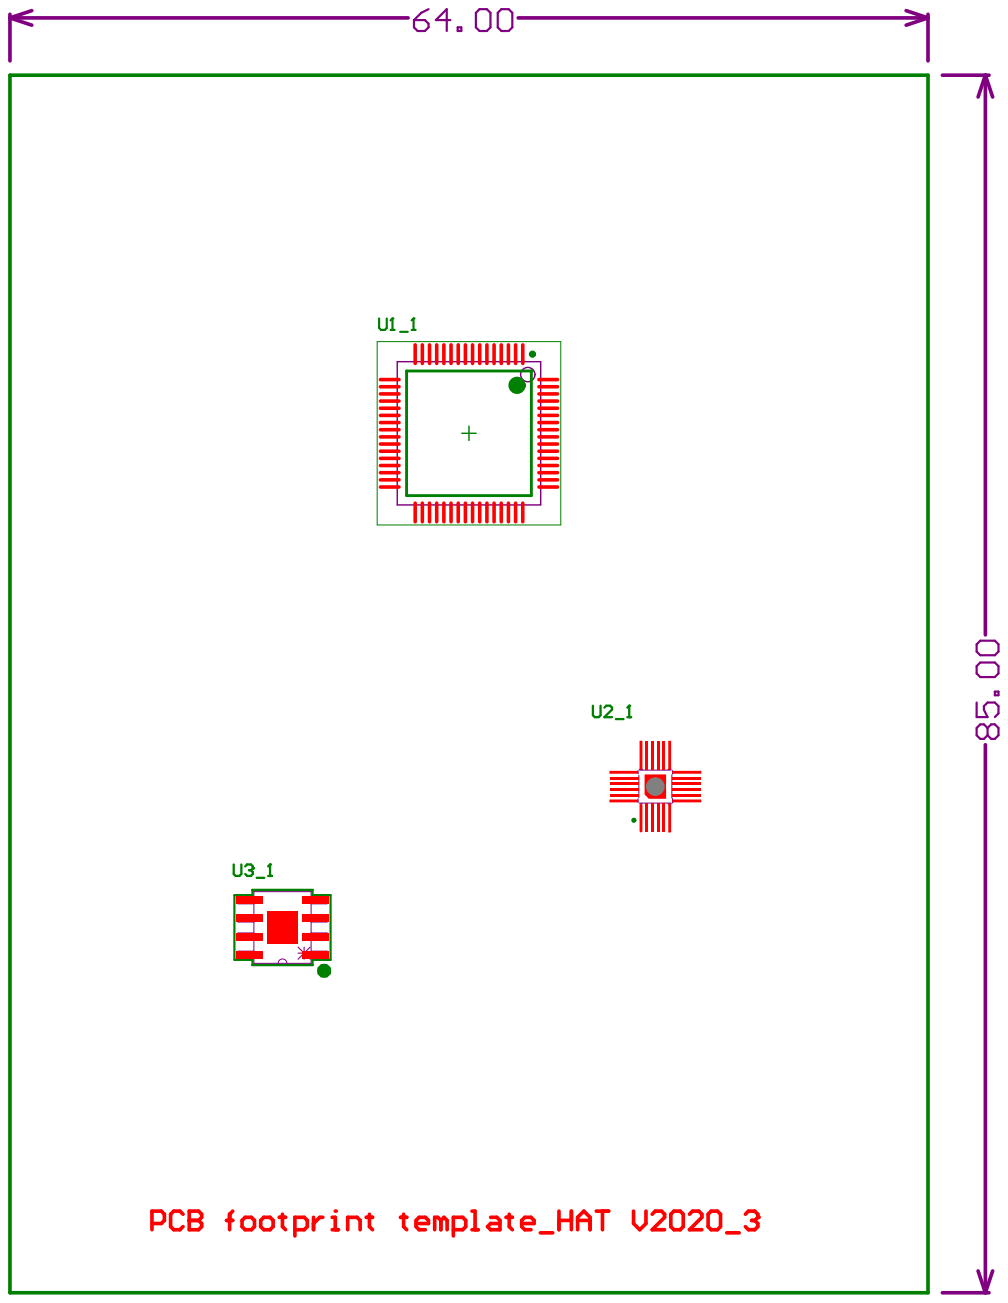
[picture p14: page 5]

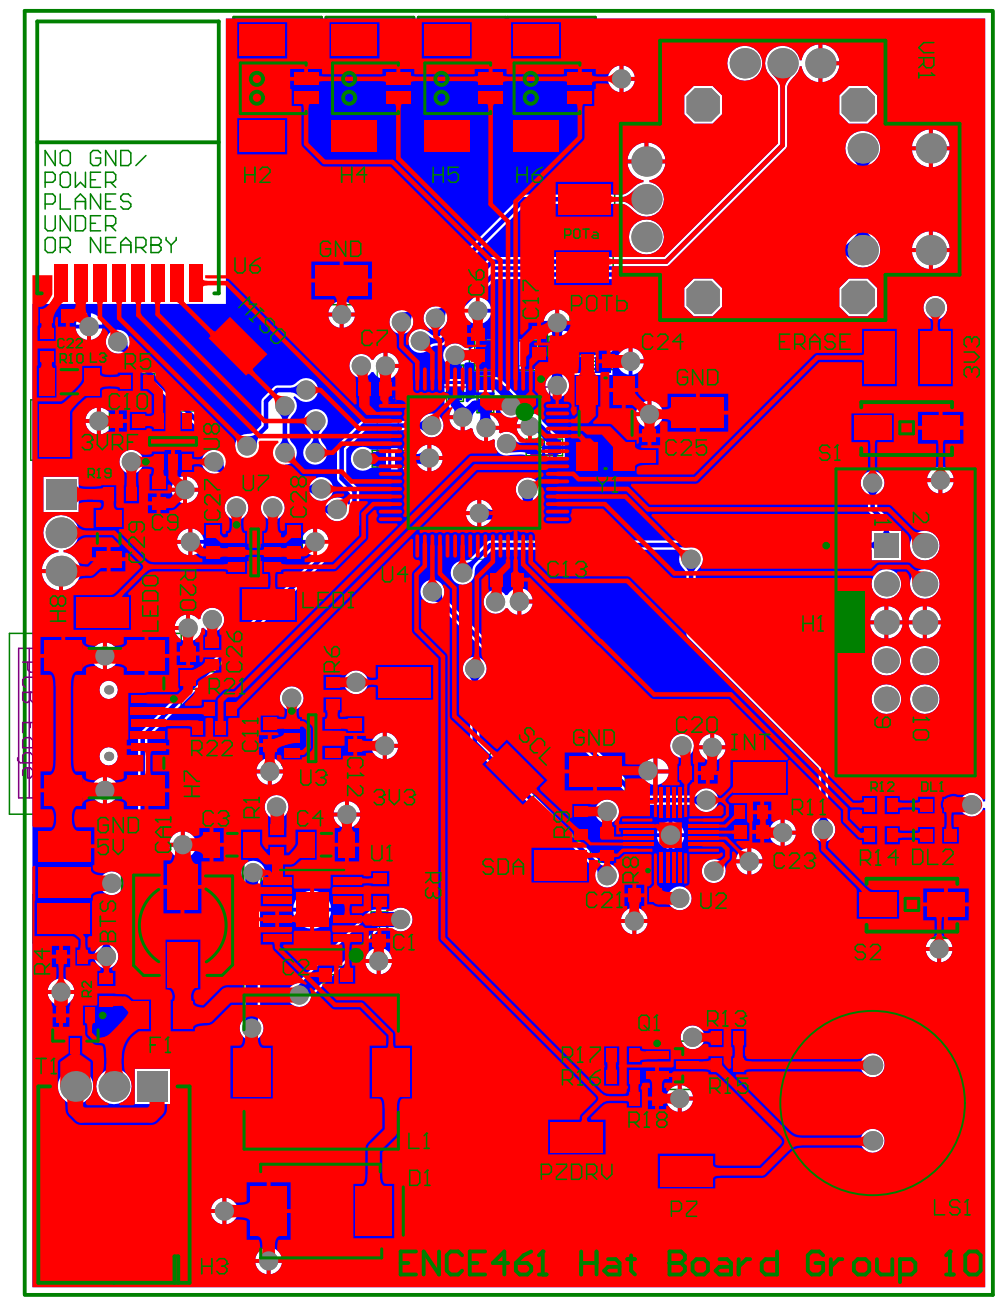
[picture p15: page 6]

Bill of Materials | Bill of Materials forProject [WackyRacesHat.PrjPcb] (No PCB Document Selected)
Source Data From: | WackyRacesHat.PrjPcb
Proj ect: | | WackyRacesHat.PrjPcb
Variant: | | None
Creation Date: 22/06/2020 | 10:42 PM
Print Date: | 22-Jun-20 | 10:42:10 PM
Footprint | Comment | LibRef | Designator | Description | Quantity
CAPC1608L 100nF | CC_100nF_0603 C1, C2, C5, C6, C7, C8, C13, C14, C15, C16, C17, C19, C20, C23 | CAP CER 100nF X7R +-10% 50V 0603 | 14
CAPC3216L 22uF | CC_22uF_1206 C3, C4, C29 | CAP CER 22uF Y5V -20% +80% 10V 1206 | 3
CAPC1608L 1uF | CC_1uF_0603 | C9, C10, C11, C12 | CAP CER 1uF Y5V -20% +80% 16V 0603 | 4
CAPC1608N 4.7uF | CC_4.7uF_0603 C18, C26 | CAP CER 4.7uF X5R +-20% 10V 0603 | 2
CAPC1608L 10nF | CC_10nF_0603 C21, C27, C28 | CAP CER 10nF X7R +-10% 50V 0603 | 3
CAPC1608L 10uF | CC_10uF_0603 C22 | CAP CER 10UF X5R +-20% 6V3 0603 | 1
CAPC1608L 27pF | CC_27pF_0603 C24, C25 | CAP CER 27pF NPO/COG +-5% 50V 0603 | 2
NICH-1 | 100uF/16V | CA_100uF_16V CA1 | CAP ALUM 100uF 16V SMD | 1
SMC | VS-30BQ015-M3/9DS_VS-30BQ015D1 | DIODE, SCHOTTKY, 3A, 15V, DO-214AB / S | 1
WL-SMCW060B right Green | DL_150060VS75DL1 | LED Bright Green 40mcd 0603 SMD | 1
WL-SMCW060Re d | DL_150060RS75DL2 | LED Red 250mcd 0603 SMD | 1
RESC3216N 5A | FS_Fuse_5.0A | F1 | Fuse 5.0A Fast Acting 1206 SMD | 1
IDC2.54-V10DHeader 5X2 Vert JA_HDR_IDC_5XH1 | IDC Header, 2,54mm, 10-Pin, Vert | 1
SD-53398-021SMD Vert 1.25mmJB_53398-02 | H2, H4, H5, H6 | Header_Vert_2Pos_1.25mm_125V@1A_SM | 4
BATT_HEADEBattery_HEADER_Battery_HEADER_H3 | 3Pin Header 2.54mm spacing | 1
USB/SM0.8-6H5JS_USB_MINI_B JS_USB_MINI_BH7 | USB 2.0, Right Angle, SMT, B Type, Recepta | 1
HEADER_3POHE ADER_3 | HEADER_3 | H8 | 3Pin Header 2.54mm spacing | 1
INDUCTOR5uIND 5.2UH 6A | CDRH104RNP-5R2L1 | FIXED IND 5.2UH 6A 22 MOHM SMD | 1
INDC3216L | 1A max, Idc 0.3R,IN_Ferrite-Bead L2, L3 | Ferrite Bead, Rdc 0.3R, Z100MHZ 600R, Ima | 2
XDCR_PS124PS1240P02BT PS1240P02BT LS1 | Buzzers Transducer, Externally Driven Piezo | 1
SOT323_M | BC817W | TB_BC817W | Q1 | NPN GP Bipolar Transistor 45V 500mA SOT | 1
RESC1608L 0R | RS_0R0 | R1, R5, R6, R11, R13, R17, R19, R20 | RES 0.0 OHM 1/10W 5% 0603 SMD | 8
RESC1608L 200K | RS_200K | R2 | RES 200K OHM 1/10W 5% 0603 SMD | 1
RESC1608L 100K | RS_100K | R3, R4 | RES 100K OHM 1/10W 5% 0603 SMD | 2
RESC3216L 1R | RT_1R | R7 | RES 1R OHM 1/4W 5% 1206 SMD | 1
RESC1608L 2K2 | RS_2K2 | R8, R9 | RES 2.2K OHM 1/10W 5% 0603 SMD | 2
RESC1608L 10R | RS_10R | R10, R16 | RES 10 OHM 1/10W 5% 0603 SMD | 2
RESC1608L 470R | RS_470R | R12 | RES 470 OHM 1/10W 5% 0603 SMD | 1
RESC1608L 680R | RS_680R | R14 | RES 680 OHM 1/10W 5% 0603 SMD | 1
RESC1608L 1K | RS_1K | R15, R18 | RES 1.0K OHM 1/10W 5% 0603 SMD | 2
RESC1608L 27R | RS_27R | R21, R22 | RES 27 OHM 1/10W 5% 0603 SMD | 2
EVQPNF05M EVQPNF05M | WS_EVQPNF05MS1, S2 | Panasonic 6 x 3.5mm SMD Light Touch Swi | 2
SOT23_L | BSH105,215 | TM_BSH105 | T1 | MOSFET N-CH 20V 1.05A SOT-23 | 1
RD_8_1 | ADP2302ARDZ-5ADP 2302ARDZ-5U1 | IC REG BUCK 5V 2A 8SOIC | 1
Quad24 | MPU-9250 | MPU-9250 | U2 | 9 axis IMU | 1
SOT95P280XCAT6219-330TDGSV_CAT6219-33U3, U8 | IC REG LIN 3.3V 500MA TSOT23-5 | 2
LQFP64_L | ATSAM4S8BA-ASE_ATSAM4S16U4 | IC MCU 32BIT 512KB FLASH 64LQFP | 1
NRF24 | nRF24 SMD | NRF24 | U6 | nRF24 SMD Module | 1
SOT23-6_N | SN74LVC1T45 | SN74LVC1T45 | U7 | 1.8V - 5V level converter | 1
Joystick_Sw Joystick 10k with Joystick 10k with VR1 | JOYSTICK 10K OHM 2 AXIS TH | 1
6.0X3.5-4 | 12MHz | XT_CRYSTAL_1Y1 | CRYSTAL 12MHZ 18PF 6X3.5mm SMD | 1
81
Approv ed | Notes

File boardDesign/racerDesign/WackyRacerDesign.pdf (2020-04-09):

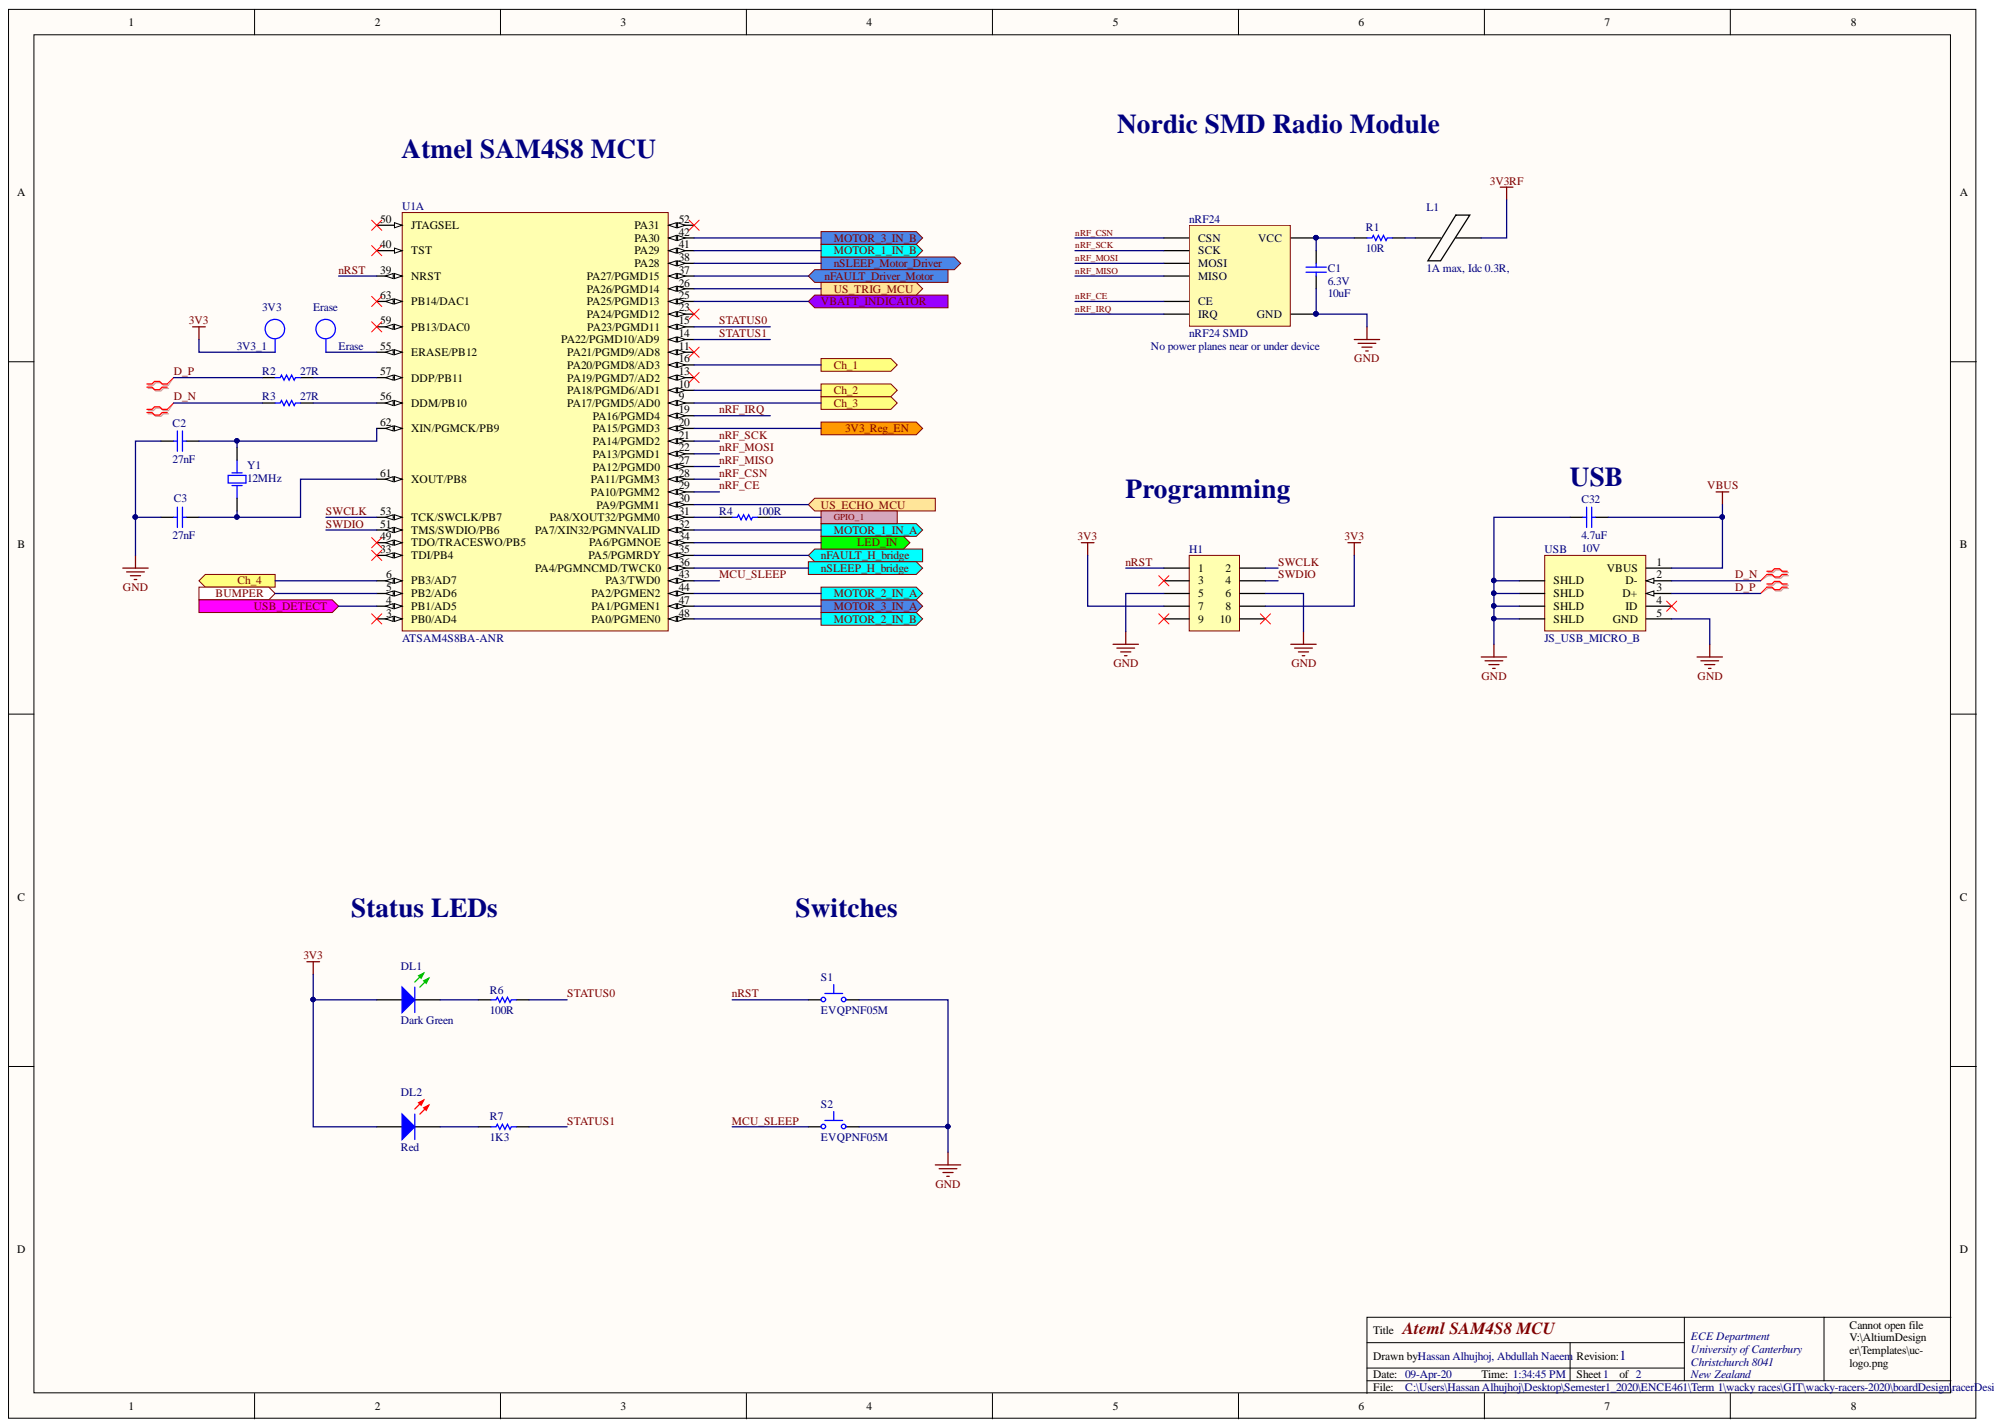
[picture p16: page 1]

Nordic SMD Radio Module

No power planes near or under device

Ateml SAM4S8 MCU Title | ECE Department University of Canterbury Christchurch 8041 New Zealand | Cannot open file V:\AltiumDesign er\Templates\uc-logo.png

Drawn by: Hassan Alhujhoj, Abdullah Naeem | Revision:
Date: 09-Apr-20 Time: 1:34:45 PM | Sheet of 2

C:\Users\Hassan Alhujhoj\Desktop\Semester1_2020\ENCE461\Term 1\wacky races\GIT\wacky-racers-2020\boardDesign\racerDesign\MCU.SchDoc

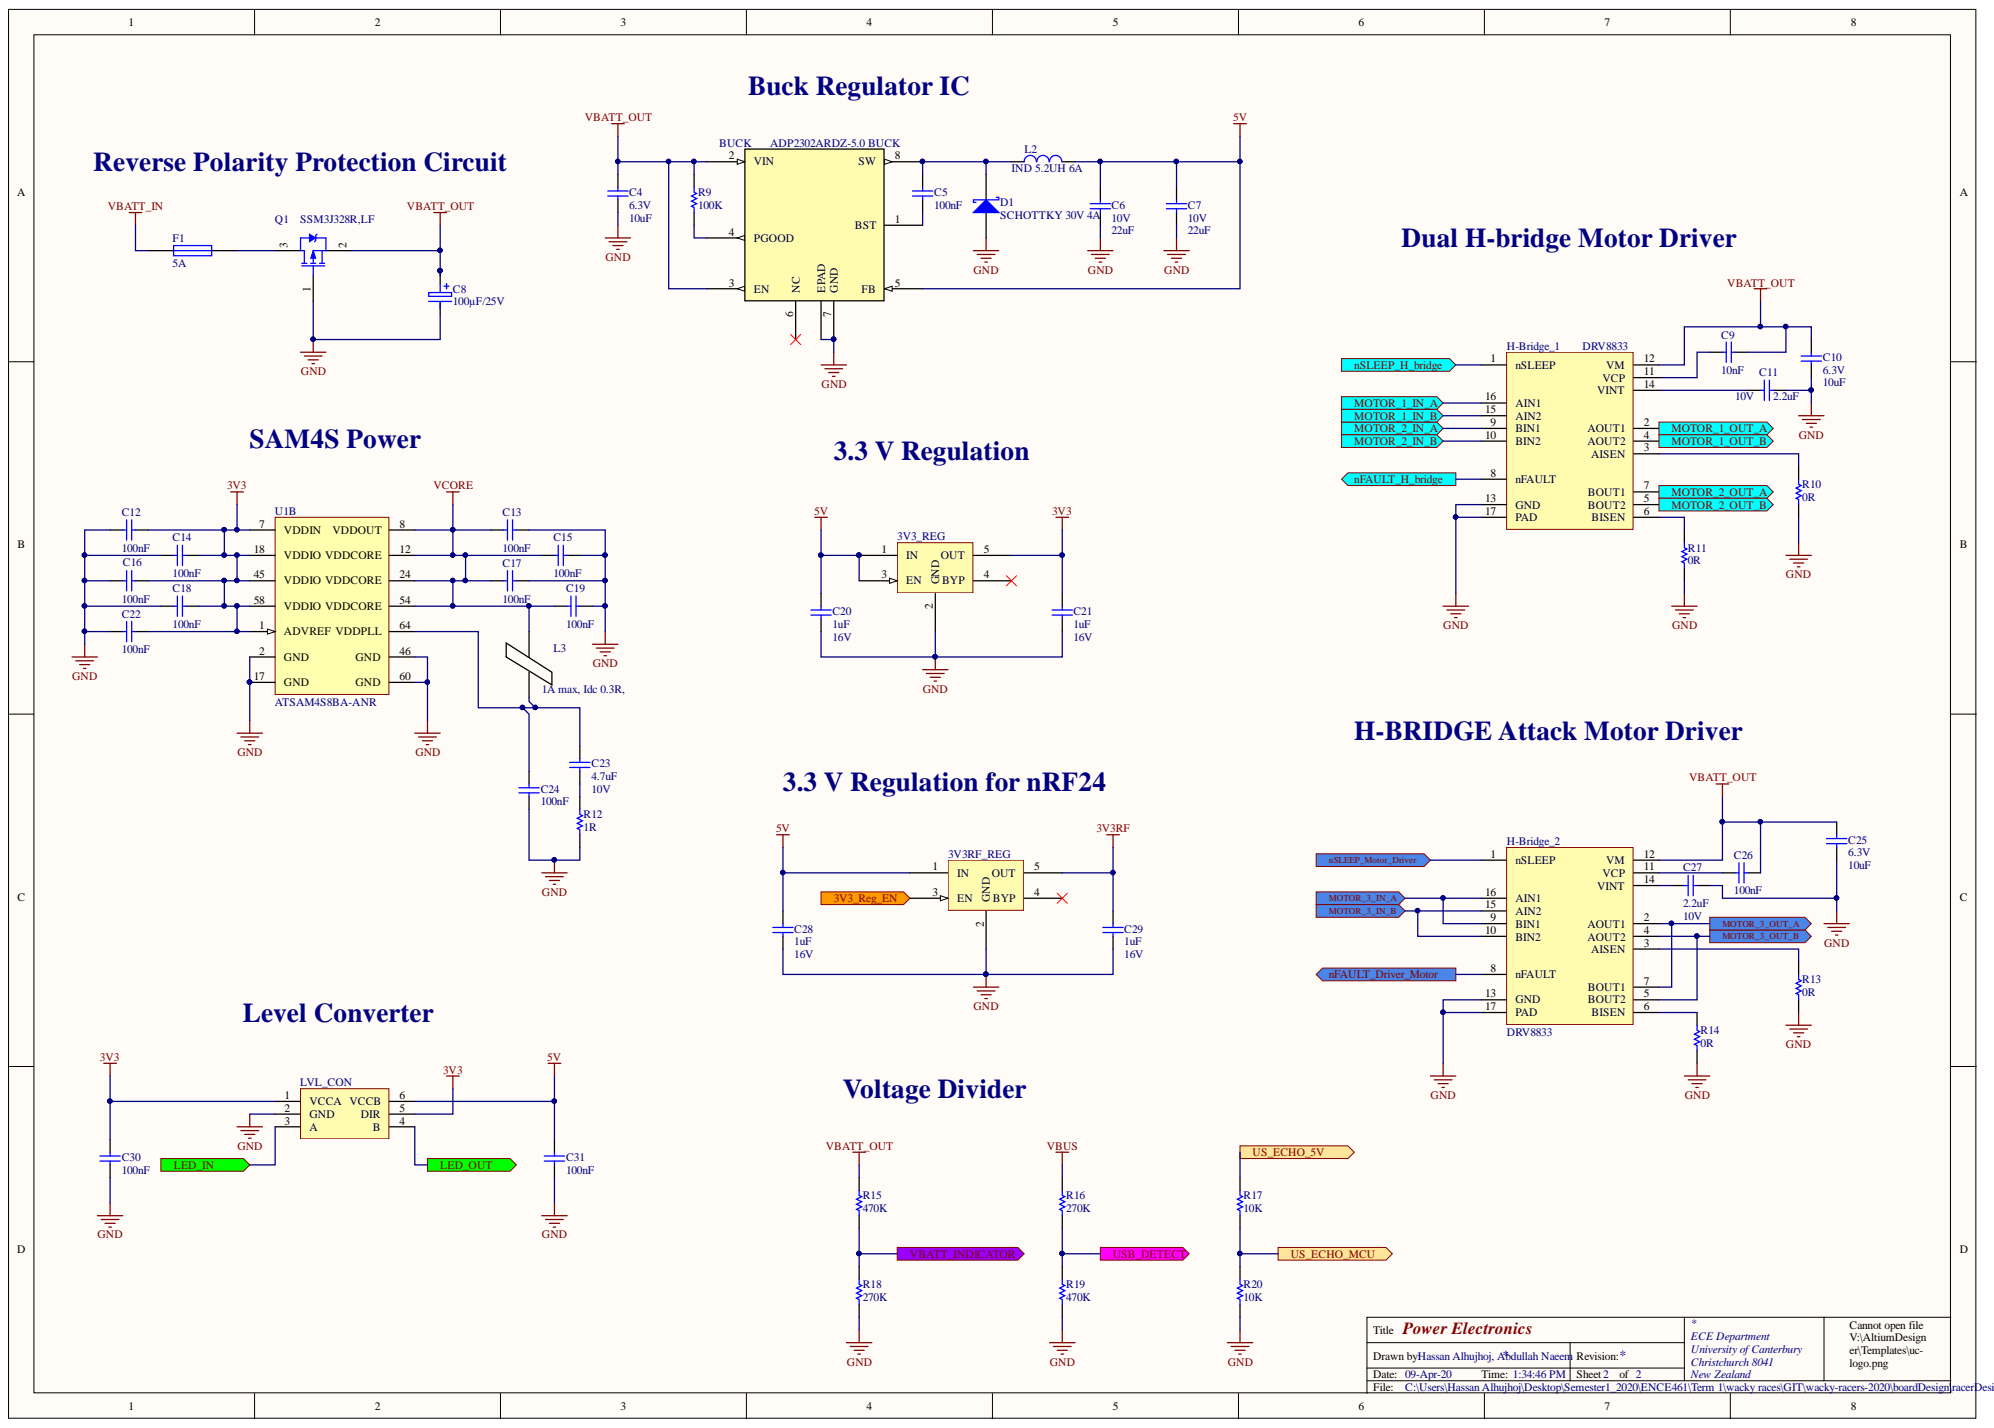
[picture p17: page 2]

Reverse Polarity Protection Circuit

Dual H-bridge Motor Driver

H-BRIDGE Attack Motor Driver

Power Electronics Title | * ECE Department University of Canterbury New Zealand | Cannot open file V:\AltiumDesign er\Templates\uc-

09-Apr-20 1:34:46 PM | 2

C:\Users\Hassan Alhujhoj\Desktop\Semester1_2020\ENCE461\Term 1\wacky races\GIT\wacky-racers-2020\boardDesign\racerDesign\Power.SchDoc

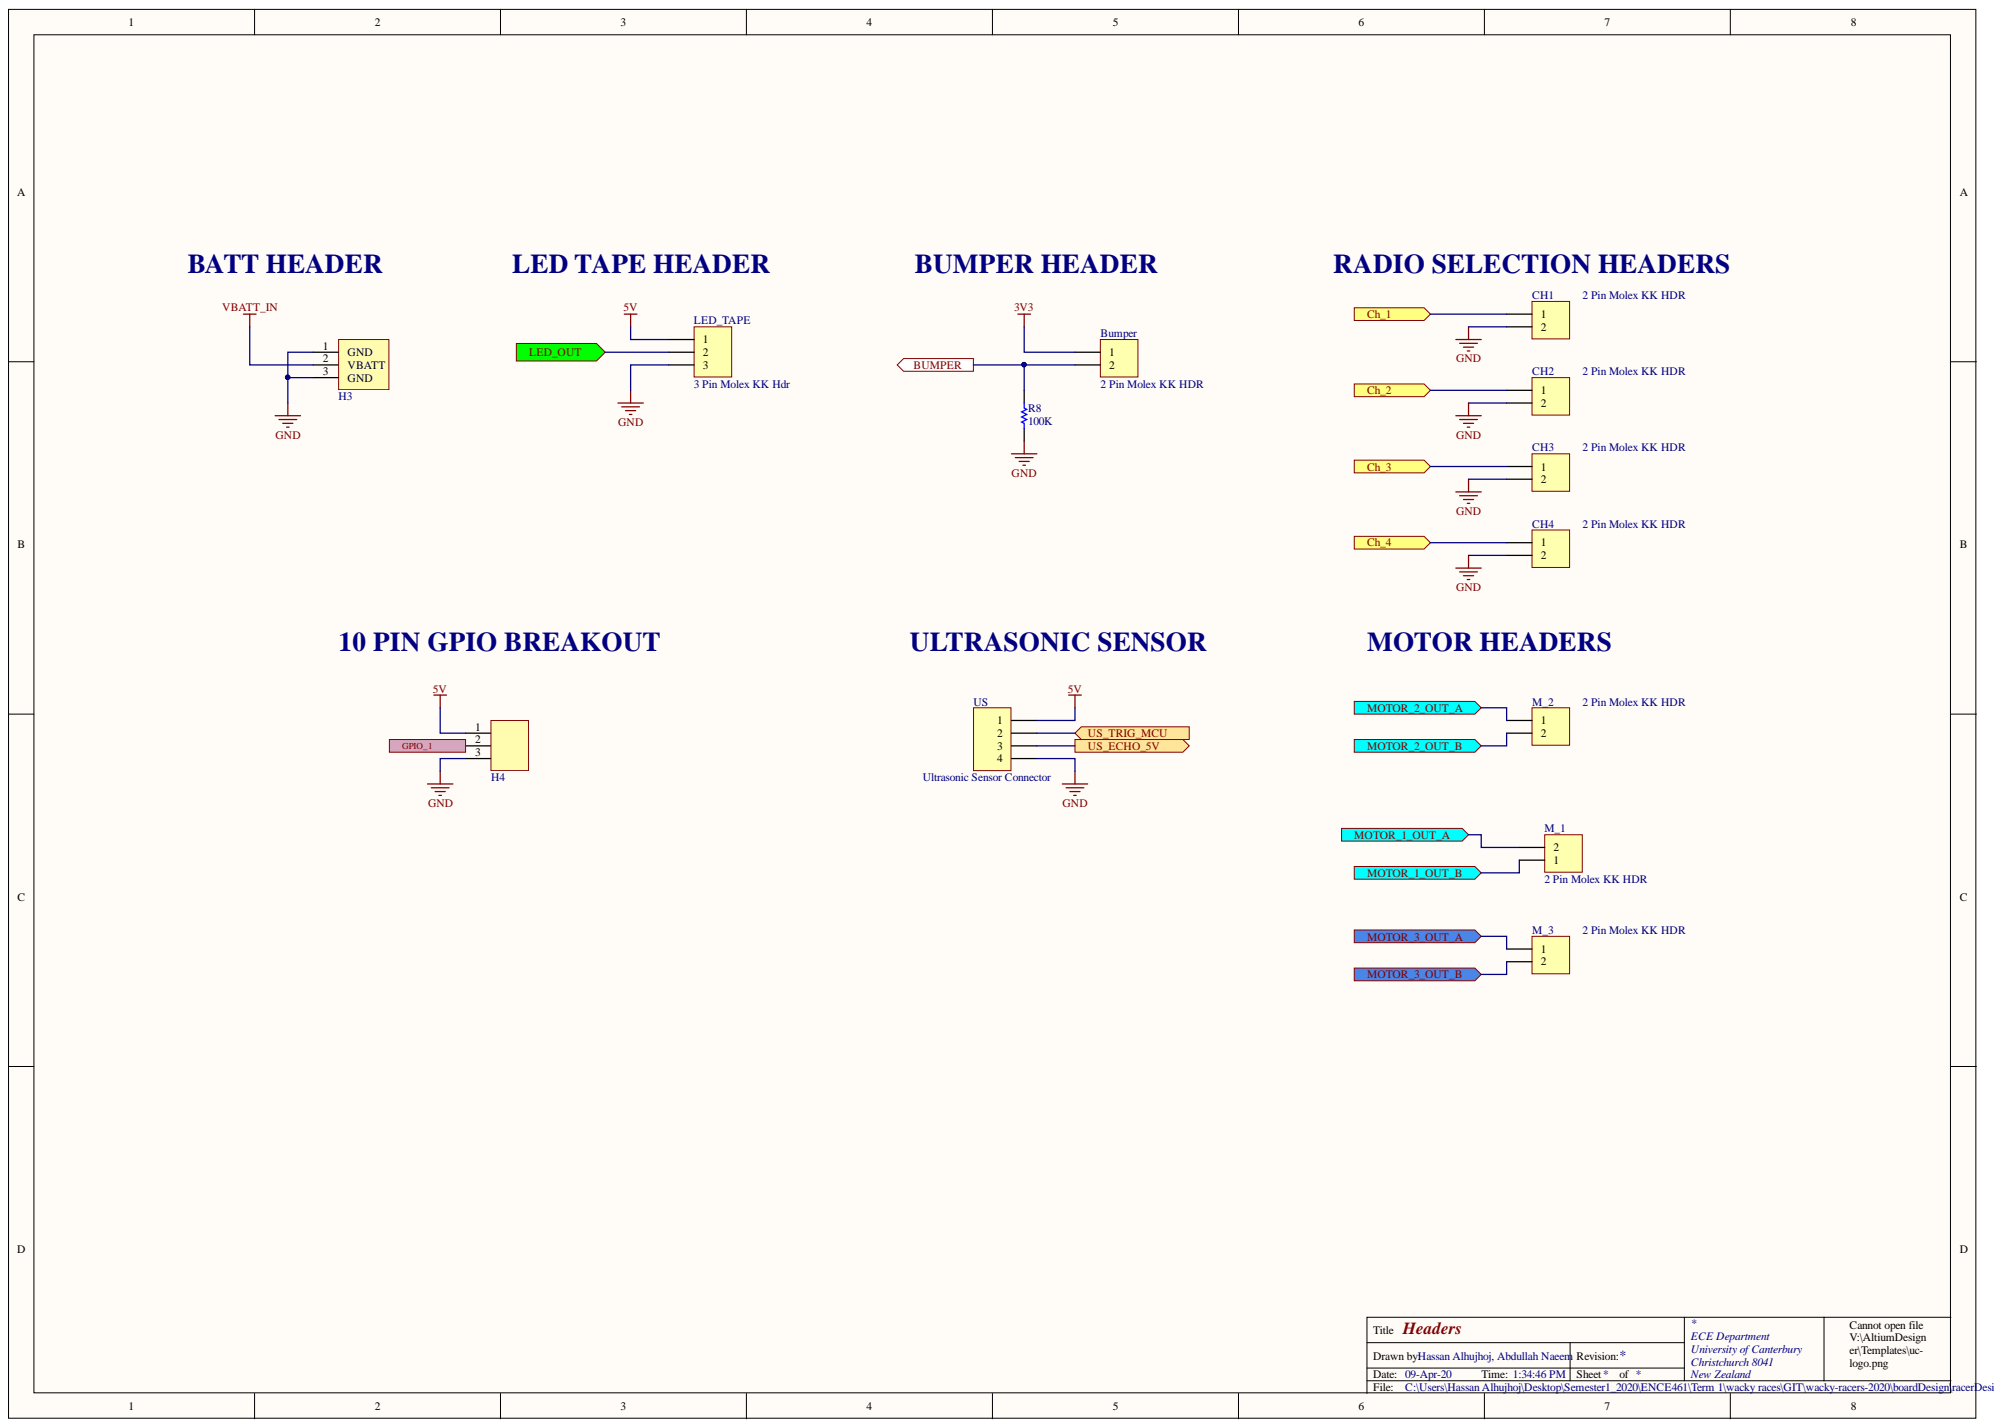
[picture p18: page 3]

2 Pin Molex KK HDR

GPIO_1 | 3

Headers Title | * ECE Department University of Canterbury New Zealand | Cannot open file V:\AltiumDesign er\Templates\uc-

C:\Users\Hassan Alhujhoj\Desktop\Semester1_2020\ENCE461\Term 1\wacky races\GIT\wacky-racers-2020\boardDesign\racerDesign\Headers.SchDoc

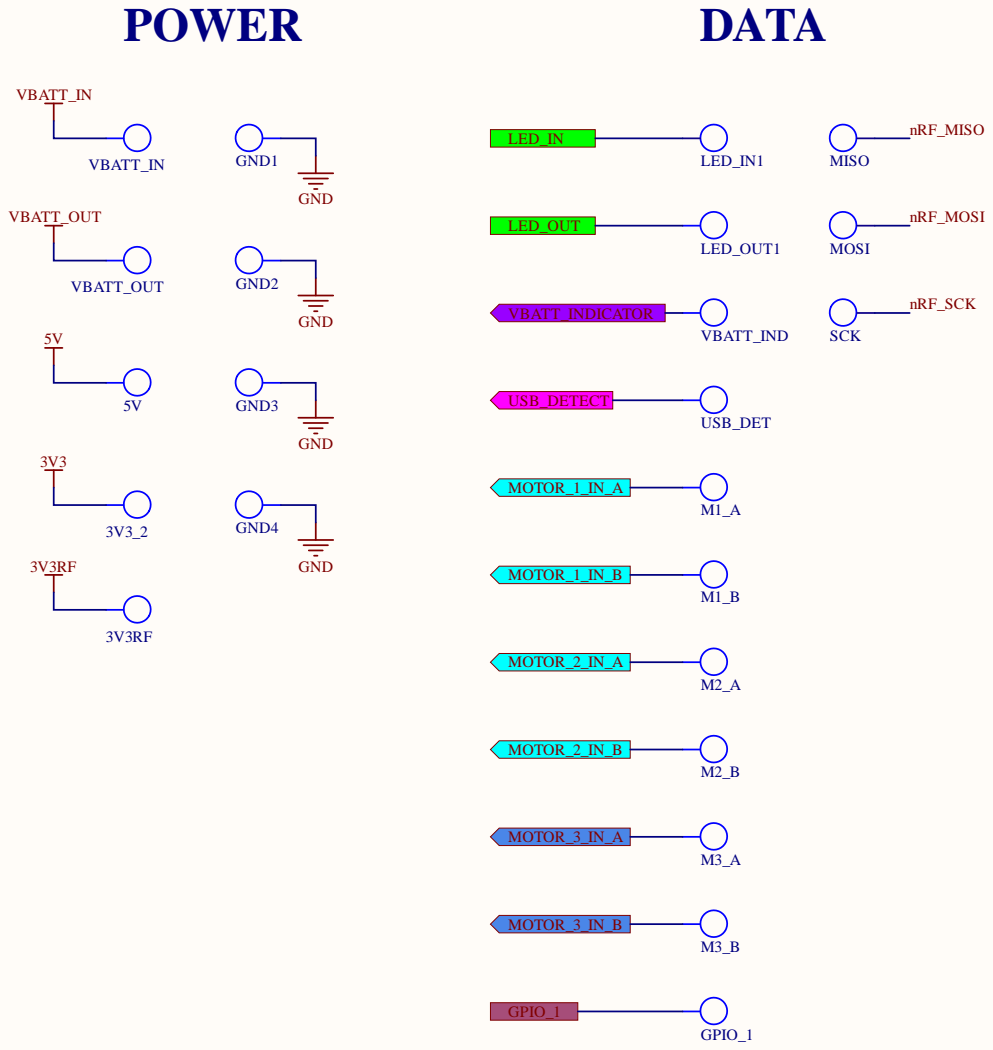
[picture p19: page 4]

C:\Users\Hassan Alhujhoj\Desktop\Semester1_2020\ENCE461\Term 1\wacky races\GIT\wacky-racers-2020\boardDesign\racerDesign\TestPoints.SchDoc

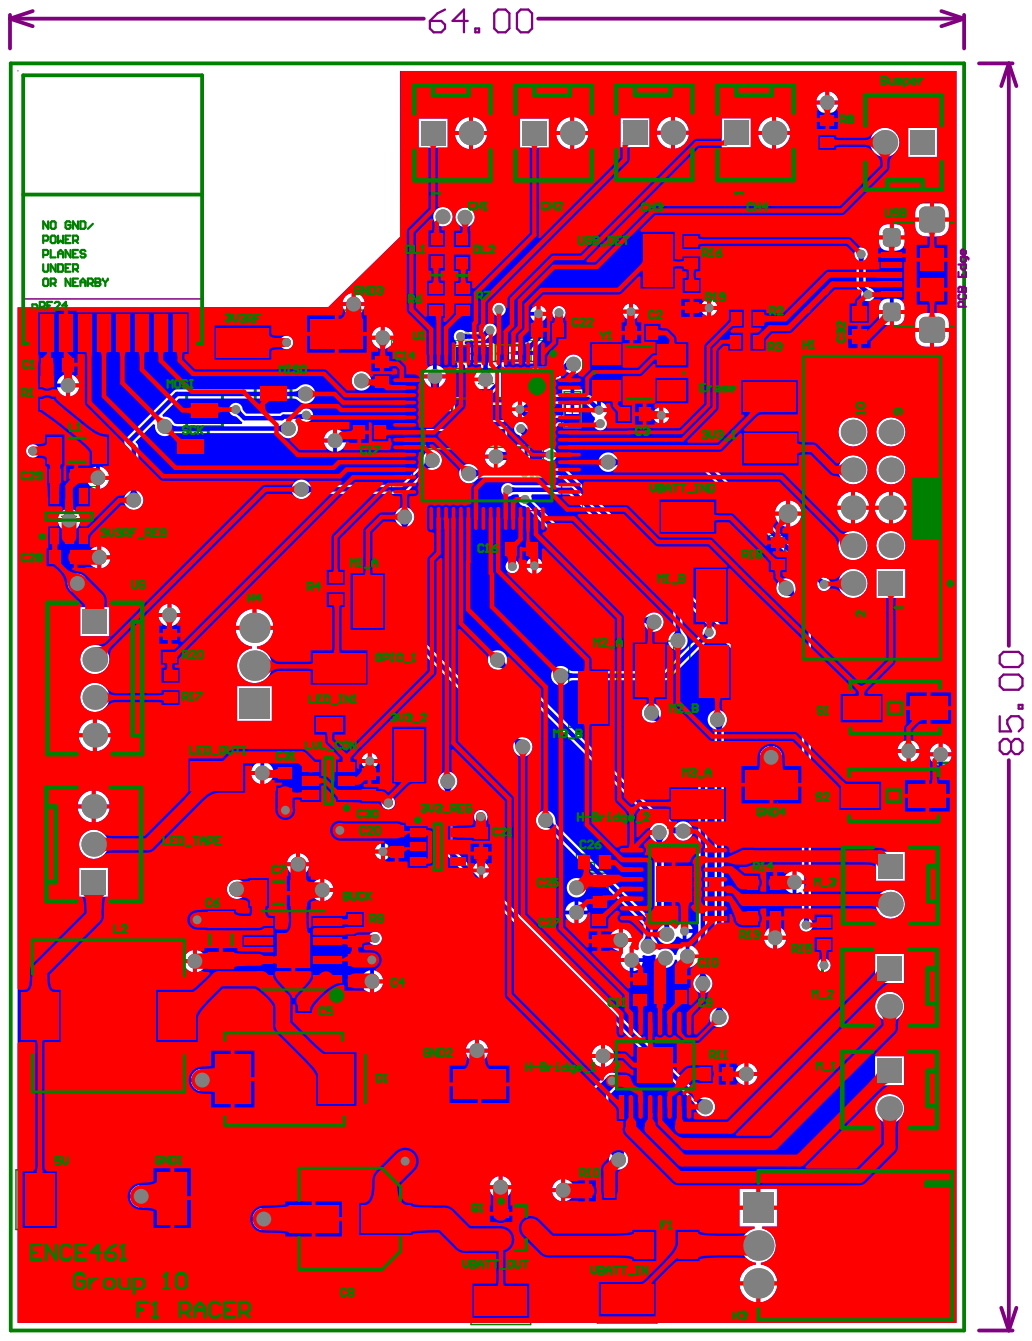
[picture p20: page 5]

# Board Stack Report

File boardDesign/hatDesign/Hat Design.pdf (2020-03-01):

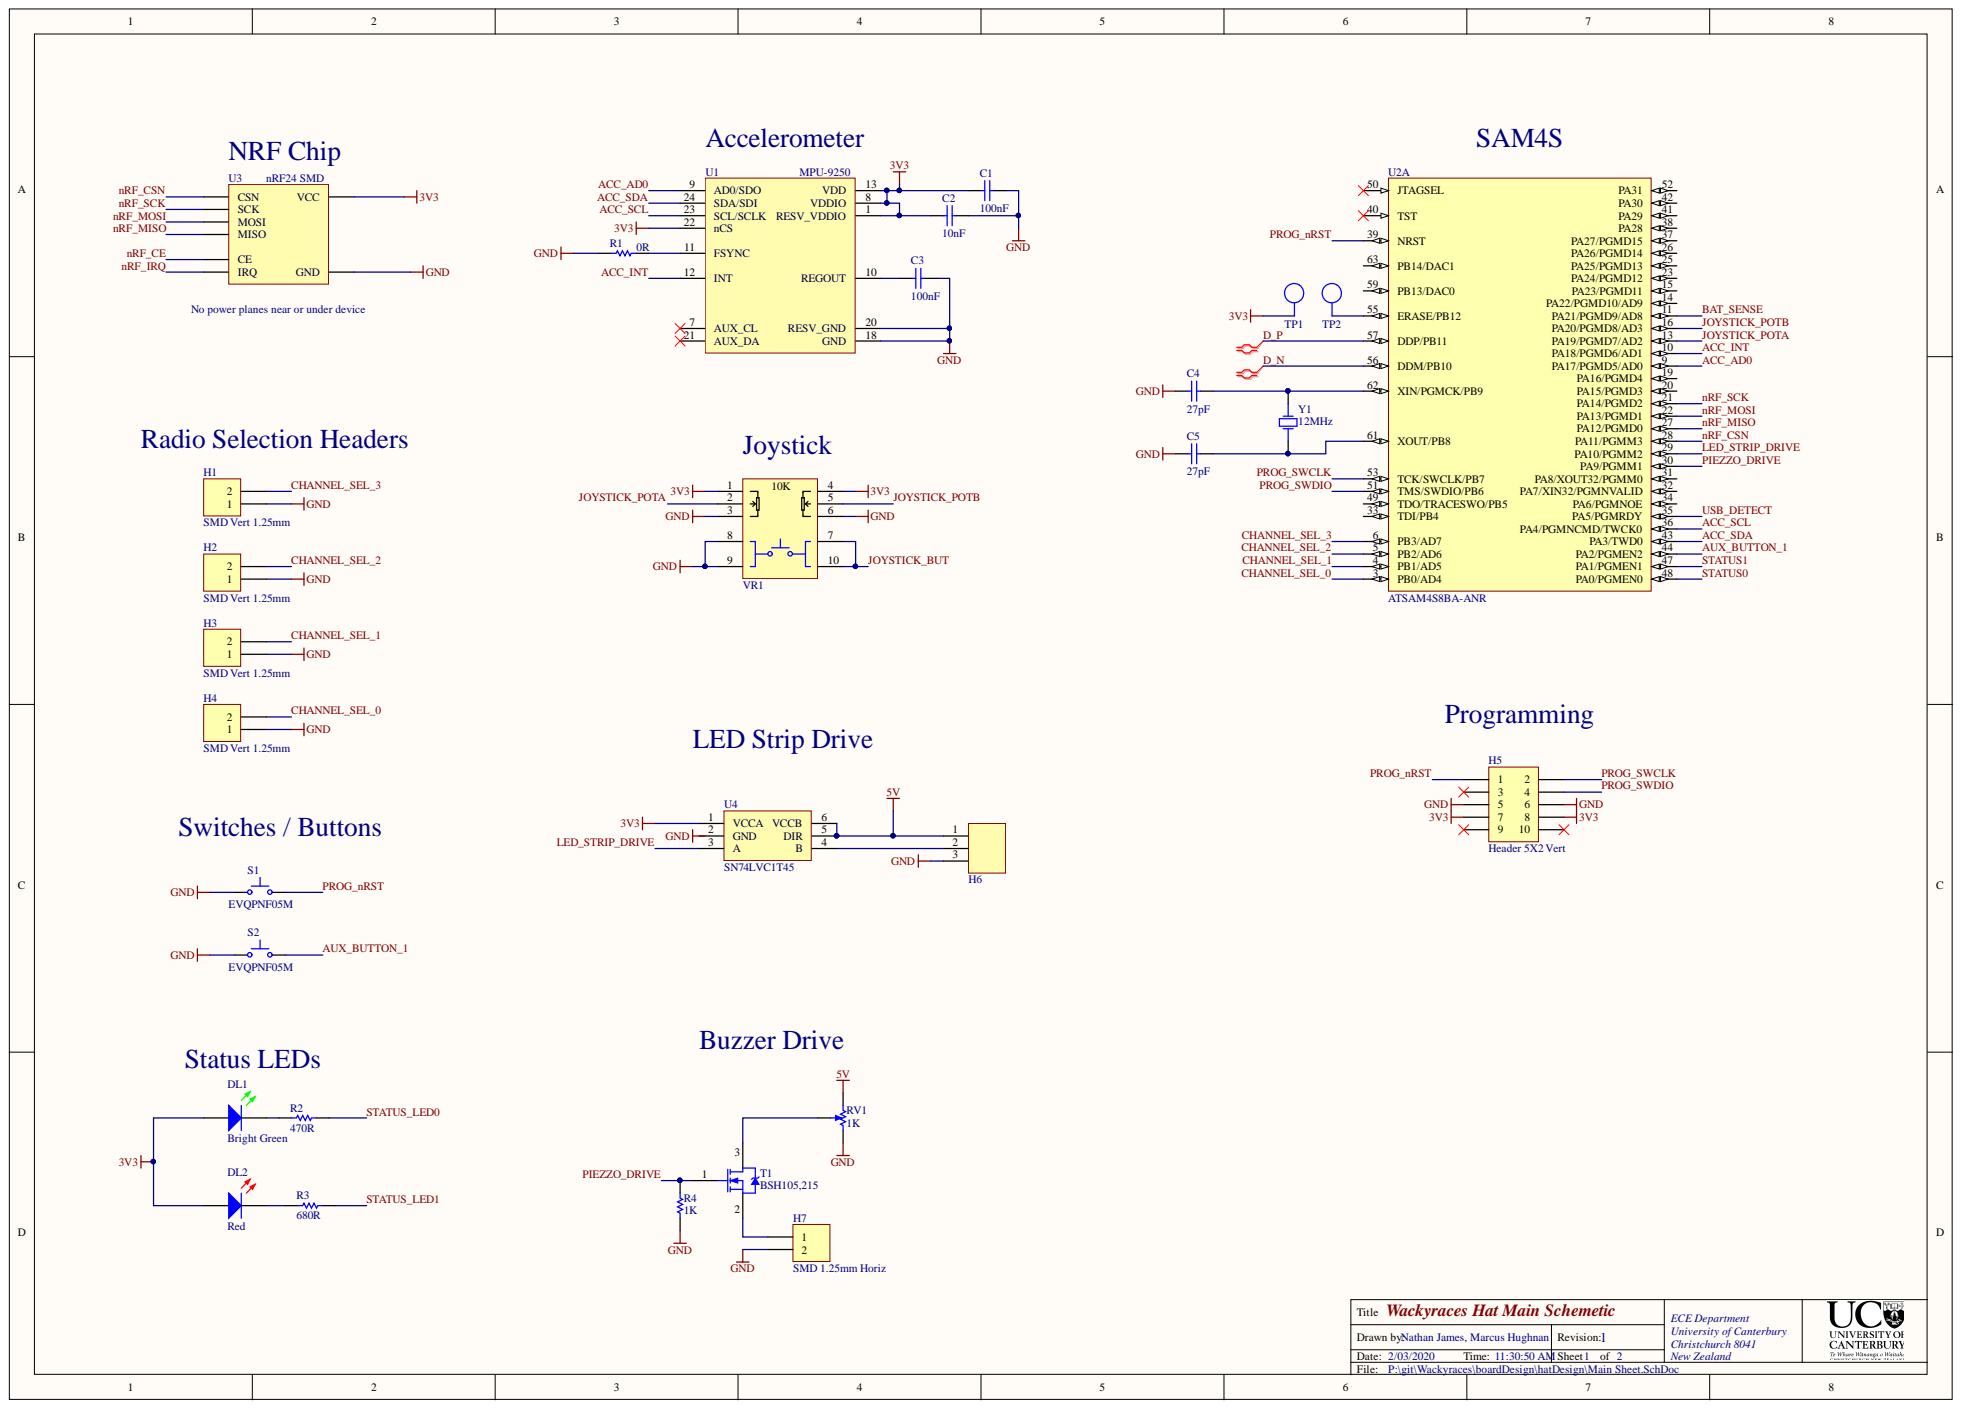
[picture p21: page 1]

No power planes near or under device

Wackyraces Hat Main Schemetic Title | ECE Department University of Canterbury Christchurch 8041 New Zealand

Drawn by: Nathan James, Marcus Hughnan | Revision: 1
Date: 2/03/2020 Time: 11:30:50 AM | Sheet 1 of 2

P:\git\Wackyraces\boardDesign\hatDesign\Main Sheet.SchDoc


VDDIO 58

GND 2

Wackyraces Hat Power Schematic Title | ECE Department University of Canterbury Christchurch 8041 New Zealand

Drawn by: Nathan James, Marcus Hughnan | Revision: 1
Date: 2/03/2020 Time: 11:30:50 AM | Sheet 2 of 2

P:\git\Wackyraces\boardDesign\hatDesign\Power Sheet.SchDoc

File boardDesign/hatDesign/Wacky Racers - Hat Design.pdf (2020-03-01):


No power planes near or under device

TODO: Find out if IRQ or CE pins are used

TODO: Test points and 0R breakpoints

TODO:Calculate resistor values using load line for 2mA
current through leds.

TODO: Rename file? is this possible

Wackyraces Hat Main Schemetic Title | ECE Department University of Canterbury Christchurch 8041 New Zealand

Drawn by: Nathan James, Marcus Hughnan | Revision: 1
Date: 2/03/2020 Time: 11:25:42 AM | Sheet 1 of 2

P:\git\Wackyraces\boardDesign\hatDesign\Tutorial Sheet.SchDoc


VDDIO 58

GND 2

Wackyraces Hat Power Schematic Title | ECE Department University of Canterbury Christchurch 8041 New Zealand

Drawn by: Nathan James, Marcus Hughnan | Revision: 1
Date: 2/03/2020 Time: 11:25:43 AM | Sheet 2 of 2

P:\git\Wackyraces\boardDesign\hatDesign\Power Sheet.SchDoc

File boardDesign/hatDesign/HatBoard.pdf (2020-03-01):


VDDIO 58

GND 2

Wackyraces Hat Power Schematic Title | ECE Department University of Canterbury Christchurch 8041 New Zealand

Drawn by: | Revision: 1
Date: 2/03/2020 Time: 10:33:35 AM | Sheet of

P:\git\Wackyraces\boardDesign\hatDesign\Power Sheet.SchDoc


No power planes near or under device

TODO: Find out if IRQ or CE pins are used

TODO: Test points and 0R breakpoints

TODO:Calculate resistor values using load line for 2mA
current through leds.

TODO: Rename file? is this possible

Wackyraces Hat Main Schemetic Title | ECE Department University of Canterbury Christchurch 8041 New Zealand

Drawn by: Nathan James | Revision: 1
Date: 2/03/2020 Time: 10:33:35 AM | Sheet of

P:\git\Wackyraces\boardDesign\hatDesign\Tutorial Sheet.SchDoc

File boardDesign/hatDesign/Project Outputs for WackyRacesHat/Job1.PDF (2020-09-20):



Comment | Description | Designator | Footprint | LibRef | Quantity
100nF | CAP CER 100nF X7R +-10% C1, C2,C5, C6, C7, C8,CAPC1608L | | | C _100n F_0603 | 14
22uF | CAP CER 22uF Y5V -20%C3, C4, C29 | | CAPC3216L | CC_22uF_1206 | 3
1uF | CAP CER 1uF Y5V -20%C9,C10, C11, C12 | | CAPC1608L | CC_1uF_0603 | 4
4.7uF | CAP CER 4.7uF X5R +-20% C18, C 26 | | CAPC1608N | CC_4.7uF_0603 | 2
10nF | CAP CER 10nF X7R +-10%C21, C27, C28 | | CAPC1608L | CC_10nF_0603 | 3
10uF | CAP CER 10UF X5R +-20%C22 | | CAPC1608L | CC_10uF_0603 | 1
27pF | CAP CER 27pF NPO/COC24, C25 | | CAPC1608L | CC_27pF_0603 | 2
100uF/16V | CAP ALUM 100uF 16V SCA1 | | NICH-1 | CA_100uF_16V | 1
VS-30BQ015-M3/9AT | DIODE, SCHOTTKY, 3AD 1 | | SMC | DS_VS-30BQ015-M3 | 1
Bright Green | LED Bright Green 40mcd DL 1 | | WL-SMCW0603 | DL_150060VS75000 | 1
Red | LED Red 250mcd 0603 DL2 | | WL-SMCW0603 | DL_150060RS75000 | 1
5A | Fuse 5.0A Fast Acting F1 | | RESC3216N | FS_Fuse_5.0A | 1
Header 5X2 Vert | IDC Header, 2,54mm, | H1 | IDC2.54-V10D | JA_HDR_IDC_5X2_VER | 1
SMD Vert 1.25mm | Header_Vert_2Pos_1.25mH2,H 4, H5, H6 | | SD-53398-0219 | JB_53398-02 | 4
Battery_HEADER_3pin3Pin Header 2.54mm spaH3 | | | BATT_HEADER_3POS | Battery_HEADER_3pin | 1
JS_USB_MINI_B | USB 2.0, Right Angle, | SH7 | USB /S M0.8-6H 5 | JS_USB_MINI_B_SMT | 1
HEADER_3 | 3Pin Header 2.54mm spaH8 | | HEADER_3POS | HEADER_3 | 1
IND 5.2UH 6A | FIXED IND 5.2UH 6A 22 L1 | | INDUCTOR5u2 | CDRH104RNP-5R2NC | 1
1A max, Idc 0.3R, | Ferrite Bead, Rdc 0.3RL2, L3 | | INDC 3216L | IN_Ferrite-Bead | 2
PS1240P02BT | Buzzers Transducer, ELS1 | | XDCR_PS 1240P02B T | PS1240P02B T | 1
BC817W | NPN GP Bipolar TransistQ 1 | | SOT323_M | TB_BC817W | 1
0R | RES 0.0 OHM 1/10W 5%R1, R5, R6,R11, R13,RE SC1608L | | | RS_0R0 | 8
200K | RES 200K OHM 1/10W R2 | | RESC1608L | RS_200K | 1
100K | RES 100K OHM 1/10W R3, R 4 | | RESC1608L | RS_100K | 2
1R | RES 1R OHM 1/4W 5%R 7 | | RESC3216L | RT_1R | 1
2K2 | RES 2.2K OHM 1/10W | R8, R9 | RESC1608L | RS_2K2 | 2
10R | RES 10 OHM 1/10W 5%R10, R16 | | RESC1608L | RS_10R | 2
470R | RES 470 OHM 1/10W 5%R12 | | RESC1608L | RS_470R | 1
680R | RES 680 OHM 1/10W 5%R14 | | RESC1608L | RS_680R | 1
1K | RES 1.0K OHM 1/10W | R15, R18 | RESC1608L | RS_1K | 2
27R | RES 27 OHM 1/10W 5%R21, R22 | | RESC1608L | RS_27R | 2
EVQPNF05M | Panasonic 6 x 3.5mm | S1,S2 | EVQPNF05M | WS_EVQPNF05M | 2
BSH105,215 | MOSFET N-CH 20V 1.05AT1 | | SOT23_L | TM_BSH105 | 1
ADP2302ARDZ-5.0 BUCIC REG BUCK 5V 2A 8SU1 | | | RD_8_1 | ADP2302ARDZ-5.0-R7 | 1
MPU-9250 | 9 axis IMU | U2 | Quad24 | MPU-9250 | 1
CAT6219-330TDGT3 | IC REG LIN 3.3V 500MAU3, U8 | | SOT95P280X145-5N | SV_CAT6219-330TDGT | 2
ATSAM4S8BA-ANR | IC MCU 32BIT 512KB FU4 | | LQFP64_L | SE_ATSAM4S16BA-MU | 1
nRF24 SMD | nRF24 SMD Module | U6 | NRF24 | NRF24 | 1
SN74LVC1T45 | 1.8V - 5V level convertU7 | | SOT23-6_N | SN74LVC1T45 | 1
Joystick 10k with Sw | JOYSTICK 10K OHM 2 AVR1 | | Joystick_Sw | Joystick 10k with Sw | 1
12MHz | CRYSTAL 12MHZ 18PF Y1 | | 6.0X3.5-4 | XT_CRYSTAL_12MHz_18pF | 1

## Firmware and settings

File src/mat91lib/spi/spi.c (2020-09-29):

/** @file   spi.c
    @author Michael Hayes
    @date   30 July 2007
    @brief  Routines for interfacing to the SPI bus.
*/

#include "config.h"
#include "spi.h"
#include "mcu.h"
#include "cpu.h"
#include "pinmap.h"
#include "bits.h"


/* This driver only configures the SPI controller as a master.

   The AT91 SPI peripheral can transmit either 8 or 16 bit data with
   MSB first.  It has 4 separate control status registers and can control
   4 different types of SPI peripheral using the separate chip select
   registers.  Each peripheral can have its own chip select that is
   automatically driven for each transfer.

   The AT91 SPI peripheral has been designed so that blocks of a data
   can be streamed using DMA to multiple devices on the bus (Variable
   Peripheral Selection).  It achieves this by using 32 bits to
   specify the 8 or 16 bit data plus a bit mask specifying which
   peripheral to write to.

   There are 4 control status registers (CSRs); one associated with
   each of the four SPI chip select (CS) signals.  These configure the
   number of bits per transfer and the CS timing for each of the 4
   channels.  The SPI controller chooses one of these 4 CSRs on the
   basis of the channel select mask in the mode register (fixed
   peripheral mode) or in the data (variable peripheral mode).  Now
   this is all fine and dandy if we have 4 SPI devices.  What if we
   want more?  Well one option is to decode the 4 CS signals to
   provide 15 channels; with four per group.  This requires external
   hardware so is not much use.  The alternative is to bit bash
   additional output ports. 

   With this driver we can share the 4 channels among multiple SPI
   devices.  However, automatic CS driving can only be performed for
   the few NPCS signals associated with a channel, otherwise the CS
   signals are bit-bashed.  If an NPCS pin is configured as an SPI
   peripheral it will be driven whenever its channel is used.  Thus if
   we want to have other CS signals driven by PIO lines, we need to
   switch the NPCS signals at the start and end of a transfer.

   There are three chip select modes: 
   SPI_CS_MODE_FRAME where the CS is asserted for multiple SPI tranmissions,
   SPI_CS_MODE_TOGGLE where the CS is only asserted for each SPI transmission, and
   SPI_CS_MODE_HIGH where the CS is kept high.

   Automatic CS driving is only used for SPI_CS_MODE_TOGGLE.  With
   SPI_CS_MODE_FRAME it is necessary to change the CSAAT bit for the
   ultimate transfer.  The additional fiddling around is not
   worthwhile.  There is only a marginal benefit using automatic chip
   select assertion.  It is primarily designed for use with DMA.

   Note, functions that configure the SPI peripheral (such as
   spi_bits_set) only take effect when spi_config is called (usually
   when some I/O is to be performed).
*/


/* Number of independent SPI controllers.  */
#ifdef SPI1
#define SPI_CONTROLLERS_NUM 2
#else
#define SPI_CONTROLLERS_NUM 1
#endif


/* Currently the maximum of SPI devices is 32 due to the size
   of the mask used for recording active devices.  */
#ifndef SPI_DEVICES_NUM
#define SPI_DEVICES_NUM 8
#endif


#ifndef HOSTED
#define HOSTED 0
#endif


/* Bit masks for the SPI mode settings.  */
enum 
{
    SPI_CPOL_MASK = BIT (0),
    SPI_NCPHA_MASK = BIT (1), 
    SPI_CSAAT_MASK = BIT (3)
};


/* Macros.  */

#ifndef SPI0
#define SPI0 SPI
#endif

#ifndef SPI1
#define SPI1 0
#endif

#define SPI_BASE_GET(channel) (((channel) < SPI_CHANNELS_NUM) ? SPI0 : SPI1)


#ifdef HOSTED
#define SPI_READY_P(BASE) (HOSTED || ((BASE)->SPI_SR & SPI_SR_RDRF))
#else
#define SPI_READY_P(BASE) ((BASE)->SPI_SR & SPI_SR_RDRF)
#endif

#define SPI_TXEMPTY_P(BASE) ((BASE)->SPI_SR & SPI_SR_TDRE)

/* Set lastxfer bit for use in fixed mode.  */
#define SPI_LASTXFER(BASE) ((BASE)->SPI_CR = SPI_CR_LASTXFER)


/* Read SPI and then send new data.  Blocks while the new data is
   being sent by the spi.  */
#define SPI_XFER(pSPI, txdata, rxdata)                                  \
    do                                                                  \
    {                                                                   \
        /* Dummy read from RDR to ensure RDRF clear.   */               \
        (rxdata) = pSPI->SPI_RDR;                                       \
                                                                        \
        /* Write data to TDR.  */                                       \
        pSPI->SPI_TDR = (txdata);                                       \
                                                                        \
        /* Wait until spi port finishes transmitting/receiving.  */     \
        while (!SPI_READY_P (pSPI))                                     \
            continue;                                                   \
                                                                        \
        /* Read new data from RDR (this clears RDRF).  */               \
        (rxdata) = pSPI->SPI_RDR;                                       \
                                                                        \
    } while (0)


static uint8_t spi_devices_num = 0;
static spi_dev_t spi_devices[SPI_DEVICES_NUM];
static spi_dev_t *spi_config_last = 0;
static uint32_t spi_devices_enabled = 0;


static inline uint32_t
spi_channel_csr_get (spi_t spi)
{
    return spi->base->SPI_CSR[spi->channel & (SPI_CHANNELS_NUM - 1)];
}


static inline void
spi_channel_csr_set (spi_t spi, uint32_t csr)
{
    spi->base->SPI_CSR[spi->channel & (SPI_CHANNELS_NUM - 1)] = csr;
}


/** Set the delay (in clocks * 32) for automatic deassertion of chip select.  */
static void
spi_channel_cs_hold_set (spi_t spi, uint16_t delay)
{
    uint32_t csr;

    csr = spi_channel_csr_get (spi);

    /* Set the DLYBCT (delay between consecutive transfers).  This is
       the only mechanism for automatically delaying the automatic
       deassertion of the chip select.  */
    BITS_INSERT (csr, delay, 24, 31);

    spi_channel_csr_set (spi, csr);
}


/** Set the delay (in clocks) to when the shift clock starts from when
    the transmit data register is written.  */
static void
spi_channel_cs_setup_set (spi_t spi, uint16_t delay)
{
    uint32_t csr;

    csr = spi_channel_csr_get (spi);

    /* Set the DLYBS (delay before SPCK).  */
    BITS_INSERT (csr, delay, 16, 23);

    spi_channel_csr_set (spi, csr);
}


/** The minimum divisor value is 1, this gives the maximum rate of MCK.  */
static void
spi_channel_clock_divisor_set (spi_t spi, spi_clock_divisor_t clock_divisor)
{
    uint32_t csr;

    csr = spi_channel_csr_get (spi);

    BITS_INSERT (csr, clock_divisor, 8, 15);

    spi_channel_csr_set (spi, csr);
}
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

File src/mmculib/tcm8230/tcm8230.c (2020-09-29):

#include "pio.h"
#include "piobus.h"
#include "pwm.h"
#include "tc.h"
#include "delay.h"
#include "i2c_master.h"
#include "tcm8230.h"

/* This driver bit-bashes a TCM8230 image sensor.  

   It assumes that the data lines D0-D7 are contiguous on the same
   port.

   I2C/TWI is required to configure the TCM8230.  This can be
   bit-bashed with any two PIO lines.

   A TC or PWM output is required to drive EXTCLK.  It appears that
   the EXTCLK frequency needs to be at least 6.25 MHz when configuring
   the TCM8230 via I2C (TWI).  The frequency of EXTCLK can then be
   reduced to allow grabbing of the data by polling a PIO port.

   When the TCM8230 is correctly configured, it will start the DCLK,
   HD, and VD signals and put the pixel data on the D0-D7 data lines.

   The TCM8230 requires three power supplies.  If the 2.5 V supply is
   not provided, all the pixels return black (97, 8) in colour
   (RGB565) mode.


   DCLK has a frequency of EXTCLK / 4.  Thus with EXTCLK at 2 MHz,
   DCLK is 500 kHz.

   Two DCLKs are required per pixel.
   
   With EXTCLK at 2 MHz, SQCIF frame format (128 x 96 pixels), and
   low-power mode:

   HD is high for 128 * 2 / 500e3 = 512 us.
   HD is low for (1560 - 128 * 2) / 500e3 = 2.61 ms.
   The HD period is 1560 / 500e3 = 3.12 ms.

   VD is high for 254 lines, 254 * 1560 / 500e3 = 792.48 ms.
   VD is low for 9 lines, 9 * 1560 / 500e3 = 28.08 ms.
   The VD period is 263 lines, 263 * 1560 / 500e3 = 820.56 ms.

   This corresponds to a frame rate of 1.22 Hz.  To achieve 15 frames
   per second requires a 25 MHz EXTCLK.

   When debugging:
   1.  Check that all the regulators are enabled to power the image sensor
       before tcm8230_init is called.
   2.  Check that EXTCLK is driven my the MCU after tcm8230_init is called.
   3.  Check that the SDA and SCL lines toggle when tcm8230_init is called.
       Three bytes should be sent from the MCU and the image sensor should
       acknowledge each.
   4.  Check the DCLK, HD, and VD signals are driven by the image sensor
       after tcm8230_init is called.
*/   
 
#define TCM8230_TWI_ADDRESS 0x3C
 
#define TCM8230_CLOCK_INITIAL 6.25e6
 
#ifndef TCM8230_CLOCK
#define TCM8230_CLOCK 2e6
#endif

#define TCM8230_HSYNC_TIMEOUT_US 10000
 
 
/* Register 0x02 control fields.  */
enum {TCM8230_FPS_30 = 0,
      TCM8230_FPS_15 = 1 << 7};
 
enum {TCM8230_ACF_50 = 0,
      TCM8230_ACF_60 = 1 << 6};

/* DCLK polarity; normal is data valid on rising edge.  */ 
enum {TCM8230_DCLKP_NORMAL = 0,
      TCM8230_DCLKP_REVERSE = 1 << 1};
 
enum {TCM8230_ACFDET_AUTO = 0,
      TCM8230_ACFDET_MANUAL = 1};
 
/* Register 0x03 control fields.  */
enum {TCM8230_DOUTSW_ON = 0,
      TCM8230_DOUTSW_OFF = 1 << 7};
 
enum {TCM8230_DATAHZ_OUT = 0,
      TCM8230_DATAHZ_HIZ = 1 << 6};
 
enum {TCM8230_PICFMT_YUV422 = 0,
      TCM8230_PICFMT_RGB565 = 1 << 1};
 
enum {TCM8230_CM_COLOR = 0,
      TCM8230_CM_BW = 1};
 
 
/* Register 0x1E control fields.  */
enum {TCM8230_CODESW_OFF = 0,
      TCM8230_CODESW_OUT = 1 << 5};
 
enum {TCM8230_CODESEL_ORIGINAL = 0,
      TCM8230_CODESEL_ITU656 = 1 << 4};
 
enum {TCM8230_HSYNCSEL_NORMAL = 0,
      TCM8230_HSYNCSEL_ALT = 1 << 3};
 
enum {TCM8230_TESTPIC_NOTOUT = 0,
      TCM8230_TESTPIC_OUT = 1 << 2};
 
enum {TCM8230_PICSEL_COLORBAR = 0,
      TCM8230_PICSEL_RAMP1 = 1,
      TCM8230_PICSEL_RAMP2 = 2};

enum {TCM8230_D_MASK1 = 1 << 6};
 
 
typedef struct tcm8230_mode_struct
{
    uint16_t width;
    uint16_t height;
} tcm8230_mode_t;


static const tcm8230_mode_t modes[] =
{
    {VGA_WIDTH, VGA_HEIGHT},
    {QVGA_WIDTH, QVGA_HEIGHT},
    {QVGA_WIDTH, QVGA_HEIGHT},
    {QQVGA_WIDTH, QQVGA_HEIGHT},    
    {QQVGA_WIDTH, QQVGA_HEIGHT},    
    {CIF_WIDTH, CIF_HEIGHT},    
    {QCIF_WIDTH, QCIF_HEIGHT},    
    {QCIF_WIDTH, QCIF_HEIGHT},    
    {SQCIF_WIDTH, SQCIF_HEIGHT},    
    {SQCIF_WIDTH, SQCIF_HEIGHT}
};
 

static const i2c_bus_cfg_t i2c_bus_cfg =
{
    .scl = TCM8230_SCL_PIO,
    .sda = TCM8230_SDA_PIO
};


static uint16_t width;
static uint16_t height;


static void
tcm8230_reg_write (i2c_t i2c, uint8_t addr, uint8_t value)
{
    i2c_master_addr_write (i2c, TCM8230_TWI_ADDRESS, addr, 1,
                           &value, sizeof (value));
}

#define TC_PRESCALE 2

static const tc_cfg_t tc_cfg =
{
    .pio = TCM8230_EXTCLK_PIO,
    .mode = TC_MODE_CLOCK,
    .frequency = TCM8230_CLOCK_INITIAL,
    .prescale = TC_PRESCALE
};


static const pwm_cfg_t pwm_cfg =
{
    .pio = TCM8230_EXTCLK_PIO,
    .period = PWM_PERIOD_DIVISOR (TCM8230_CLOCK_INITIAL),
    .duty = PWM_DUTY_DIVISOR (TCM8230_CLOCK_INITIAL, 50),
    .align = PWM_ALIGN_LEFT,
    .polarity = PWM_POLARITY_LOW
};


int tcm8230_init (const tcm8230_cfg_t *cfg)
{
    tc_t tc;
    pwm_t pwm;
    i2c_t i2c;
    uint8_t value;

    if (cfg->picsize > TCM8230_PICSIZE_SQCIF_ZOOM)
        return 0;

    width = modes[cfg->picsize].width;
    height = modes[cfg->picsize].height;

    /* Configure PIOs.  */
    pio_config_set (TCM8230_VD_PIO, PIO_INPUT);
    pio_config_set (TCM8230_HD_PIO, PIO_INPUT);
    pio_config_set (TCM8230_DCLK_PIO, PIO_INPUT);

#ifdef TCM8230_RESET_PIO
    pio_config_set (TCM8230_RESET_PIO, PIO_OUTPUT_LOW);
#endif
 
    piobus_config_set (TCM8230_DATA_PIOBUS, PIO_INPUT);
 

    /* Generate EXTCLK.  Try TC then fall back to PWM driver.  */
    pwm = 0;
    tc = tc_init (&tc_cfg);
    if (tc)
    {
        tc_start (tc);
    }
    else
    {
        pwm = pwm_init (&pwm_cfg);
        if (!pwm)
            return 0;
        pwm_start (pwm);
    }
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

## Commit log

2020-02-26 Adding files of the board design to the Git Repository
    [BOM Dual Supplier Links_V2.xlsx, BOM External Suppliers.xlsx, Circuit_Labs_4Layer-85 X 80mm.PcbDoc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]
2020-02-26 Hassan's racer board design commited to git
    [MCU.SchDoc, Power.SchDoc, schematic_tutorial.PrjPcb]
2020-02-27 Fixed buttons/switches pulldown. Added Power testpoints. TODO: LED resistor value calculations Low Battery indicator LED Battery Fuse LED Strip logic / driver circuit Buzzer
    [Power Sheet.SchDoc, Tutorial Sheet.SchDoc]
2020-02-27 Added power monitoring functionality (needs values to be reviewed) Added Battery fuse Added LED strip logic Added Header for Buzzer to PIO Pin TODO: LED resistor value calculations Review Nathans cir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
    [Power Sheet.SchDoc, Tutorial Sheet.SchDoc]
2020-02-27 Changes to be committed:
    [Headers.SchDoc, MCU.SchDoc, Power.SchDoc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]
2020-03-01 Marcus' changes to Nathan's work on the hat design
    [Power Sheet.SchDoc, Tutorial Sheet.SchDoc]
2020-03-01 Cleanup and Exported PDF
    [Power Sheet.SchDoc, Tutorial Sheet.SchDoc]
2020-03-01 Changed ready for schematic submission via pdf format
    [Main Sheet - Comments.SchDoc, Main Sheet.SchDoc, Power Sheet.SchDoc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]
2020-03-04 Changes made from review of Schematic Sheet by tutors
    [Main Sheet.SchDoc, Power Sheet.SchDoc]
2020-03-04 Added template hat board to pcb design, components in. Part 1 of PCB tutorial pdf
    [Main Sheet.SchDoc, Power Sheet.SchDoc, Tutorial.PrjPcb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]
2020-03-04 Changed all the mistakes that are on the racer schematics
    [Headers.SchDoc, MCU.SchDoc, Power.SchDoc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]
2020-03-04 Added components to PCB and onto placement now
    [Main Sheet.SchDoc, Power Sheet.SchDoc, hat_template 2020V3.PcbDoc]
2020-03-04 '/p/Semester1_2020/ENCE461/Term 1/wacky races/GIT/wacky-racers-pcb/schematic_tutorial.pdf' '/p/Semester1_2020/ENCE461/Term 1/wacky races/GIT/wacky-racers-pcb/schematic_tutorial.PrjPcb' '/p/Semester1_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
    [Headers.SchDoc, MCU.SchDoc, Power.SchDoc]
2020-03-04 Added components to PCB and onto placement now (retry)
    [Main Sheet.SchDoc, WackyRacesHat.PrjPcb, WackyRacesHat.sdf]
2020-03-09 Finished Schematic for Hat Board including test points, Piezo Buzzer and other tidy ups required
    [Connections.SchDoc, Main Sheet.SchDoc, Power Sheet.SchDoc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]
2020-03-11 Finished component placement on board for hat design, needs to be reviewed and routed
    [Main Sheet.SchDoc, hat_template 2020V3.PcbDoc]
2020-03-11 I added testPoints for (a)PWR Rails (b)I2C connections (c)PWM ports (d)USB in a seperate sheet. I have also added a few decoupling caps on the reverse volt circuit. Next I need to add decoupling caps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
    [Headers.SchDoc, MCU.SchDoc, Power.SchDoc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]
2020-03-12 PCB Layout Review. Minor schematic changes
    [Connections.SchDoc, Main Sheet.SchDoc, Power Sheet.SchDoc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]
2020-03-12 Finished and corrected the schematic design. About to start the PCB tutorial now
    [Headers.SchDoc, MCU.SchDoc, Power.SchDoc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]
2020-03-12 Added the pcb layout and matched the 3 footprints
    [MCU.SchDoc, Power.SchDoc, WackyRacerDesign.PrjPcb]
2020-03-13 My brain cannot work anymore so I'm going home cuz Altium is diving me crazy
    [Headers.SchDoc, MCU.SchDoc, Power.SchDoc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]
2020-03-13 pcb progress
    [Headers.SchDoc]
2020-03-13 added pcb to git
    [car_pcb.PcbDoc]
2020-03-14 Abudullah please pull my project
    [Power.SchDoc, WackyRacerDesign.PrjPcb, car_pcb.PcbDoc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]
2020-03-14 progreess in pcb
    [Headers.SchDoc, MCU.SchDoc, Power.SchDoc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]
2020-03-14 started the routing of the PCB
    [Power.SchDoc, TestPoints.SchDoc, WackyRacerPCB.PcbDoc]
2020-03-15 PCB under heavy contruction. Not the best layout
    [Power.SchDoc, TestPoints.SchDoc, WackyRacerPCB.PcbDoc]
2020-03-17 continued routing
    [Headers.SchDoc, MCU.SchDoc, TestPoints.SchDoc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]
2020-03-17 keep going!
    [MCU.SchDoc, Power.SchDoc, WackyRacerPCB.PcbDoc]
2020-03-17 Made Major changes to PCB layout
    [Headers.SchDoc, MCU.SchDoc, Power.SchDoc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]
2020-03-18 Fixed most of the errors. Pb4-PB12 cannot be used as GPIO pins. I've created nickdown polygons to fit all the traces on the two H-bridges to fit the 0.8 mm routes
    [Headers.SchDoc, MCU.SchDoc, Power.SchDoc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]
2020-03-19 Final check on pcb done by me. Can you guys double check it please before I submit
    [Headers.SchDoc, WackyRacerPCB.PcbDoc]
2020-03-19 Added teardrop and fixed few violations
    [WackyRacerDesign.PrjPcb, WackyRacerPCB.PcbDoc]
2020-03-19 Added colour to pdf
    [MCU.SchDoc, WackyRacerDesign.PrjPcb, WackyRacerPCB.PcbDoc]
2020-03-19 made the differential pair connentions closer togather
    [WackyRacerPCB.PcbDoc]
2020-03-19 Added the polygon fill to our PCB
    [WackyRacerPCB.PcbDoc]
2020-03-19 Added the polygon pour to our PCB
    [WackyRacerPCB.PcbDoc]
2020-03-19 Fixed all the silk mistakes and all the vias that are on or too close to the silk
    [WackyRacerPCB.PcbDoc]
2020-04-09 Test push and commit from my personal laptop.
    [WackyRacerDesign.PrjPcb, WackyRacerPCB.PcbDoc]
2020-09-20 Wacky Racers 2020 - Racer and Hat Designs
    [BOM_Racer.xls, Connections.SchDoc, HatBoard_Group10.PcbDoc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]
2020-09-29 added a wiki folder
    [WackyRacerDesign.PrjPcb, WackyRacesHat.PrjPcb, WackyRacesHat.sdf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]
